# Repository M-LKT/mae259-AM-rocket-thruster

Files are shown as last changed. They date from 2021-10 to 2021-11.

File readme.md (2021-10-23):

# Goals for today

- Discussing Rocket Sizing Theory

- Determining Sizing Constraints for Rocket
    - Vehicle size (thrust)
        - Fully Fueled Mass
            - 1200 + 100 + 100 = 1400 t = 1,400,000 kg
        - Lenght
            - Length 50 m
            - Diameter 9 m

        - 0.3 rad/s^2

    - Machine print size (dimensions)
        - LaserTec 65
            - 28.9 in
            - 25.6 in
            - 22 in
            - 1322 

- Chemsitry
    - Propellants
    - Pressure

- Engine Contour Sizing
    - Chamber contour
    - Parabolic nozzle
    - Estimate for heat transfer

# Notes

Types of propellants

## Fuels (when with LOX)

- Kerosene (250-350s)
- Liquid Methane (300-380s)
- Liquid Hydrogen (400-460s)

- UDMH [Hydrazine] (250-300s)
    - monoprop (150-200s)

## Oxidizers

- Liquid Oxygen
- H202
- N20

- N2H4 [Dinitrogen Tetroxide]

# Assumptions about modeling rocket engine

- Isentropic process
- Use the Area-Mach equation to correlate gas properties throughout nozzle as a function of cross-sectional area (depends on isentropic gamma ratios)

- exhaust velocity equation

# Contour

Generated Contour
- Has regen section and a radiative nozzle extention section
- config file for RPA (evaluative copy)

Contour represents the inner surface of the rocket engine that our chamber has to meet.

# Components and CAD

For a summary of best practices and different design types, reference [This NASA Report](https://ntrs.nasa.gov/api/citations/19770009165/downloads/19770009165.pdf)

## Cooling regimes

We are choosing two cryogenic propellants in an autogenous pressurization scheme for in-space service. Therefore, the rocket engine has three distinct chamber sections.
- Fuel Jacket (LCH4 cooled section)
- Oxidizer Jacket (LOX cooled section)
- Nozzle extension (radiatively cooled high emmisivity coated refractory metal section)

The rocket engine heat supplies the energy needed to maintain pressure in the tanks. The control valves that actually feed propellant vapor back to the tanks is not in the scope of this project, so we will roughly estimate how much heat is needed for each propellant and design the cooling sections lengths based on that and an estimate of heat flux through the engine.

    Propellants recieve an equal ratio of total Q per their heat of vaporization. Where Q_fuel/h_vap_LCH4 = Q_ox/h_vap_LOX

Fuel is typically used in the chamber while a secondary oxygen section is added in the nozzle. Each section will have its own inlet and outlet, and its own cooling channel geometry.

## Chamber design

The chamber will roughly be composed of two material layers.

- Inner wall (with cooling channel geometry)
- Outer wall

### Inner wall

The inner wall needs to maintain a heat flux from the hot gases into the coolant fluid (LCH4 or LOX). It also needs to maintain pressure (the cooling jacket is approximately 20-30% higher pressure than the chamber due to injector pressure drop) in the jacket. The design parameters are:

- Material choice
    - High conductivity
    - High service temperature
    - High yeild strength at temperature (for thinness)
- Material thickness (or thickness profile)
    - Thinner = more heat flux

Material needs to also be alloyable with the outer wall material or they need to be the same material.

Cooling channel design is a complex problem, so we will simplify it basing the thickness on the worst case heating and bulk energy capacity without considering convective or cold side boundary layer effects (like nucleate boiling). With this simplification, the cooling channel design parameters become:

- Cooling channel width
- Cooling channel height (also expressible as an aspect ratio of width)
- Number of cooling channels

As mentioned above, the cooling channels must support the max expected heat flux at the worst point and the fluid must be able to support the bulk energy gain throughout the jacket without exceeding the boiling point at pressure. Jacket pressure drop effects and multiphase flow will not be considered.

### Outer wall

The outer wall is basically the pressure bearing structure of the chamber. It is optimized for weight. Design points:

- Material choice
    - Strength to weight ratio
- Material thickness

A safety factor of 1.15 is standard in stress. Loading condition: hoop stress, combined non-uniform pressure vessel stress. Vibration effects neglected.

## Inlet Outlet

Fuel jacket inlet is a external manifold at the bottom of the cooling section
Fuel jacket outlet is an internal manifold at the top of the engine to interface with injector

Oxidizer jacket inlet is an external manifold at the bottom of the printed engine
Oxidizer jacket outlet is an external manifodl at the top of the cooling section

Manifolds need to have a tapered profile to reduce static pressure variation over the jacket crossection.

## Nozzle extension

The nozzle extension design points are:
- Material choice
- Material thickness (or variable thickness profile)
- Coating material and thickness

These three parameters govern maximum equillibrium temperature, the pressure stress, and the thermal expansion stress on the components.

## Nozzle extension interface

The nozzle extension interface is the attach method between the 3D printed chamber and the nozzle extension. Roughly speaking, it needs to:

- Be manufacturable and easy to assemble with a semi-automated method
- Form a gas-vaccuum seal (pressure differential of less than 1 atm)
- Be thermally-compatible: maintain seal and not over-stress either component during the thermal expansion of the nozzle.
- Needs to withstand vibration and be flight-certifiable (if using fasteners, need lockwire probably)

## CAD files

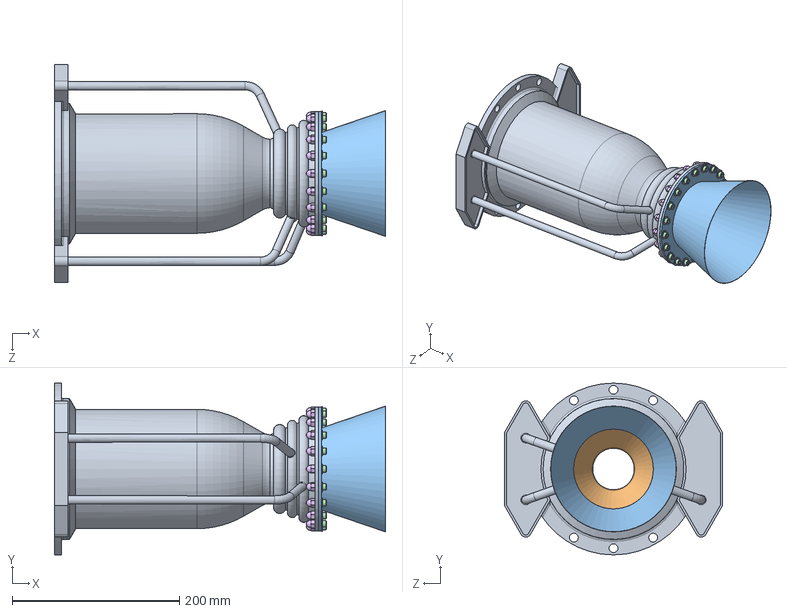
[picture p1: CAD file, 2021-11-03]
CAD_Models/Engine_Assembly.SLDASM
395.8 x 205.5 x 260.7 mm
Chamber - Outer
Chamber - Inner
Extension Nozzle
socket head cap screw_ai x 20
flat washer type a selected narrow_ai x 20
acorn low crown nut_ai x 20

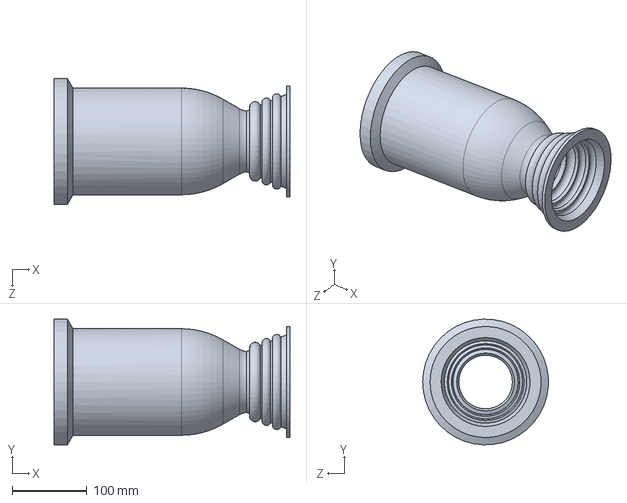
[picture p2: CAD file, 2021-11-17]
CAD_Models/DED_Adjustments/DED - Chamber - Outer.SLDPRT
315.9 x 168.3 x 168.2 mm

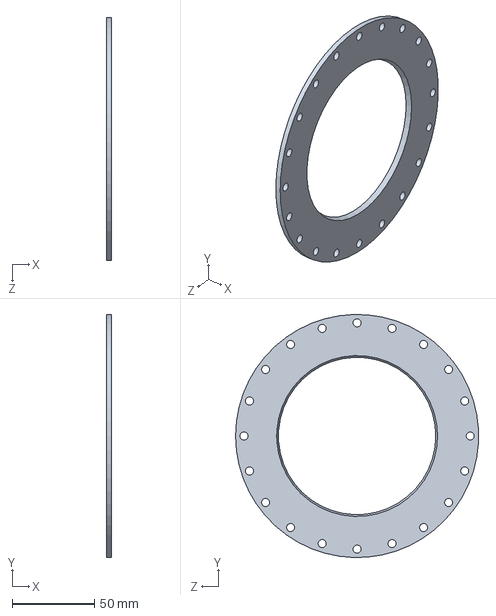
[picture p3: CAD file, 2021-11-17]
CAD_Models/ExtensionNozzleFlange_Cam.SLDPRT
3.17 x 148.1 x 148.1 mm

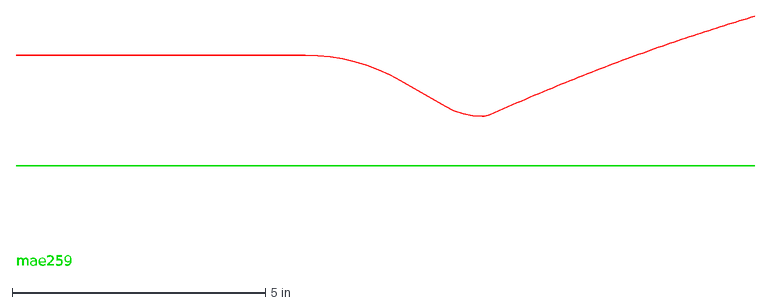
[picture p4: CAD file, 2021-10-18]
rpa-contour.dxf
mae259

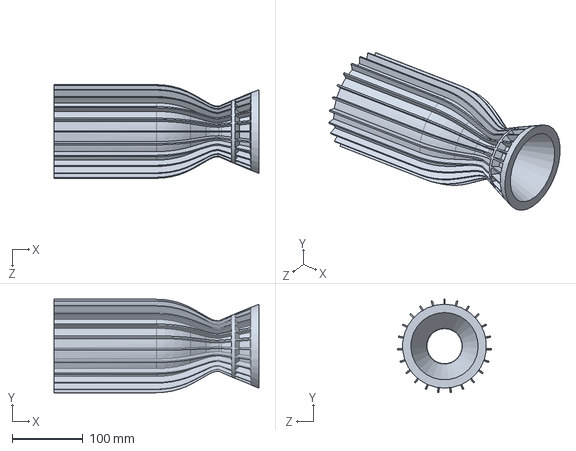
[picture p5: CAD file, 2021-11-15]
CAD_Models/Chamber - Inner.SLDPRT
290.5 x 132.5 x 132.8 mm

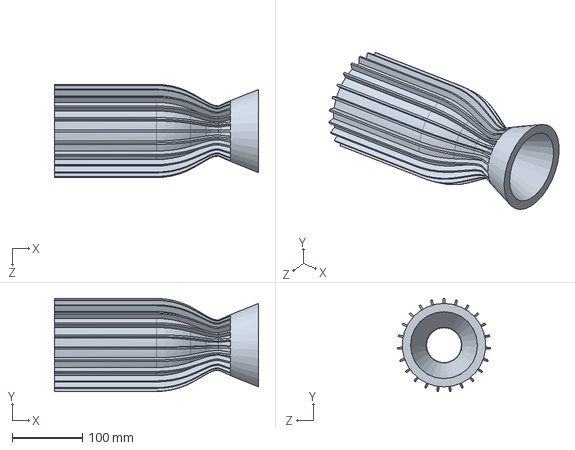
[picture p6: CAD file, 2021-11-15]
CAD_Models/DED_Adjustments/DED - Chamber - Inner.SLDPRT
290.5 x 132.5 x 132.8 mm

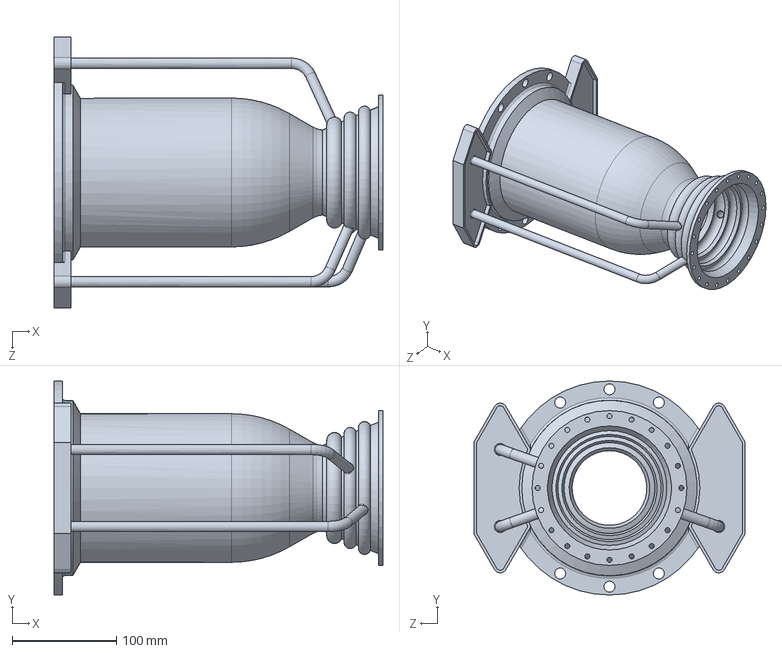
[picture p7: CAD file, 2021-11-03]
CAD_Models/Chamber - Outer.SLDPRT
315.9 x 205.5 x 260.7 mm

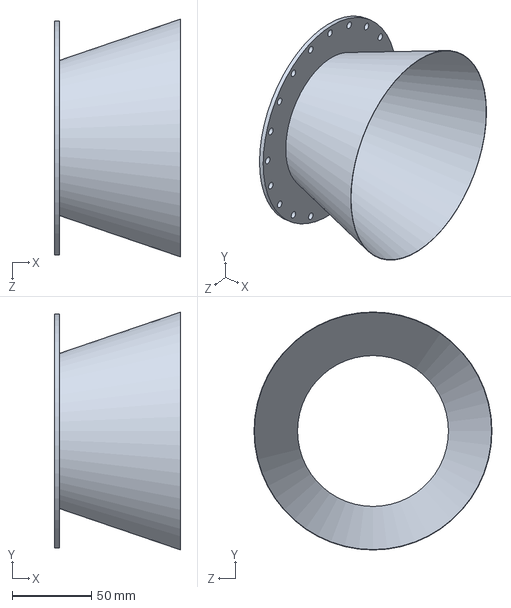
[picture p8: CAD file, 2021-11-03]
CAD_Models/Extension Nozzle.SLDPRT
80.0 x 150.4 x 150.4 mm

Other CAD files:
CAD_Models/contour.SLDPRT

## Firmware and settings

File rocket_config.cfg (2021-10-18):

version = 1.3;
name = "mae259";
info = "";
generalOptions : 
{
  multiphase = true;
  ions = true;
  flowSeparation = true;
};
combustionChamberConditions : 
{
  pressure : 
  {
    value = 6.0;
    unit = "bar";
  };
};
nozzleFlow : 
{
  calculateNozzleFlow = true;
  nozzleInletConditions : 
  {
    contractionAreaRatio = 5.0;
  };
  nozzleExitConditions : 
  {
    pressure : 
    {
      value = 0.1;
      unit = "atm";
    };
  };
  nozzleStations = ( );
};
propellant : 
{
  components : 
  {
    ratio : 
    {
      value = 3.1;
      unit = "O/F";
    };
    oxidizer = ( 
      {
        name = "O2(L)";
        massFraction = 1.0;
        p : 
        {
          value = 0.0;
          unit = "MPa";
        };
      } );
    fuel = ( 
      {
        name = "CH4(L)";
        massFraction = 1.0;
        p : 
        {
          value = 0.0;
          unit = "MPa";
        };
      } );
  };
};
engineSize : 
{
  thrust : 
  {
    value = 2.0;
    unit = "kN";
  };
  ambientConditions : 
  {
    value = 0.0;
    unit = "atm";
  };
  chambersNo = 1;
  chamberGeometry : 
  {
    length : 
    {
      value = 1.0;
      unit = "m";
    };
    characteristicLength = true;
    contractionAngle = 30.0;
    R1_to_Rt_ratio = 1.5;
    Rn_to_Rt_ratio = 0.382;
    R2_to_R2max_ratio = 0.5;
  };
};
chamberCooling : 
{
  heatTransfer : 
  {
    relationsType = "Bartz";
    applyBLC = false;
    numberOfStations = 50;
    radiationHeatTransfer : 
    {
      hotSideWallSurfaceEmissivity = 0.8;
    };
    wallLayerHeight = 0.025;
  };
  chamberCoolingSections = ( );
  filmSlots = ( );
};
propelantFeedSystem : 
{
  estimateDryMass = false;
};

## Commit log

2021-10-18 contour draft + rpa file
    [contour.SLDPRT, rocket_config.cfg, rpa-contour.dxf]
2021-10-20 finished contour design
    [contour.SLDPRT, contour_long.SLDPRT]
2021-10-23 design plan update
    [contour_long.SLDPRT]
2021-10-28 Update mae252_rocket_engine_project.m
    Added calculation for the heat flux qw and code to print out the dimensions of the cooling channel.
2021-10-28 Create Chamber - Outer.SLDPRT
    Started modeling the outer shell of the chamber. Aiming to match one of the pics Makar dropped in Discord when we met on Monday. Offset 2mm from where I expect inner wall/ribs to be but can adjust as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
    [Chamber - Outer.SLDPRT]
2021-10-29 Update Chamber - Outer.SLDPRT
    Added the "base" for mounting. Need to model inlet/outlet. Going to look into more doc's on this. I believe (2) need to attach to the nozzle?
    [Chamber - Outer.SLDPRT]
2021-10-29 Added Cooling Channels
    Added cooling channels to the rocket engine. Redid some sizing with parametric modeling. Inner-wall thickness, outer-wall thickness, cooling channel dimension, number of cooling channels can be chang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
    [Chamber - Cooling Channel.SLDPRT, Chamber - Outer.SLDPRT]
2021-10-29 added materials + started assembly
    [Chamber - Cooling Channel.SLDPRT, Chamber - Outer.SLDPRT, Engine_Assembly.SLDASM]
2021-10-29 Reconstructed Outer Geometry
    Reconstructed the outer geometry on the rocket engine with cooling channel based off of the previous geometry in Chamber - Outer part.
    [Chamber - Cooling Channel.SLDPRT]
2021-10-29 Moved Solidworks Files to CAD Folder
    [Chamber - Cooling Channel.SLDPRT, Chamber - Outer.SLDPRT, Engine_Assembly.SLDASM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]
2021-11-01 Update Chamber - Outer.SLDPRT
    Fixed the inner diameter issue so it should align with the cooling channels now. Added the inlet/outlet holes for now. Currently thinking fuel dia. will be 22.2mm and Ox dia. will be 11.1mm
    [Chamber - Outer.SLDPRT]
2021-11-02 Updated Chamber
    Updated chamber inner wall and cooling channel geometry, and added a rib seperating the 2 coolants.
    [Chamber - Cooling Channel.SLDPRT, Chamber - Inner.SLDPRT, Chamber - Outer.SLDPRT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]
2021-11-02 Update Chamber - Outer.SLDPRT
    Updated manifolds to prepare for inlet/outlet. Added potential chamber for connection below nozzle extension cutoff. Added prelim interface, not sure of sizing
    [Chamber - Outer.SLDPRT]
2021-11-02 Update Chamber - Outer.SLDPRT
    Trying to update this darn file lol
    [Chamber - Outer.SLDPRT]
2021-11-02 Update Chamber - Outer.SLDPRT
    Added in all 3 flow channels, made sure they're hollowed out. Should be good for "final" assembly unless other changes are required
    [Chamber - Outer.SLDPRT]
2021-11-02 Create Extension Nozzle.SLDPRT
    Cad for Extension Nozzle
    [Extension Nozzle.SLDPRT]
2021-11-02 Moved rib location
    [Chamber - Inner.SLDPRT, Chamber - Outer.SLDPRT, Engine_Assembly.SLDASM]
2021-11-02 Update Engine_Assembly.SLDASM
    Nozzle Added
    [Engine_Assembly.SLDASM]
2021-11-02 added material properties to nozzle extension
    [Engine_Assembly.SLDASM, Extension Nozzle.SLDPRT]
2021-11-02 Update Chamber - Outer.SLDPRT
    Added holes to nozzle interface
    [Chamber - Outer.SLDPRT]
2021-11-03 Adjust the hole for fasteners
    [Chamber - Inner.SLDPRT, Chamber - Outer.SLDPRT, Engine_Assembly.SLDASM]
2021-11-03 applied copper to inner chamber
    [Chamber - Inner.SLDPRT]
2021-11-03 Include Fasteners
    [Chamber - Inner.SLDPRT, Chamber - Outer.SLDPRT, Engine_Assembly.SLDASM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]
2021-11-03 Reapplied copper to inner chamber
    [Chamber - Inner.SLDPRT, Engine_Assembly.SLDASM]
2021-11-03 Added coolant tubes
    [Chamber - Inner.SLDPRT, Chamber - Outer.SLDPRT, Engine_Assembly.SLDASM]
2021-11-03 Added fillets cooling pipes
    Added 1mm fillets to the cooling pipes.
    [Chamber - Inner.SLDPRT, Chamber - Outer.SLDPRT, Engine_Assembly.SLDASM]
2021-11-15 Modified rocket engine geometry for DED
    [Chamber - Inner.SLDPRT, DED - Chamber - Inner.SLDPRT, DED - Chamber - Outer.SLDPRT]
2021-11-17 G-Code for DED
    [DED - Chamber - Outer.SLDPRT]
2021-11-17 Flange CAM
    [ExtensionNozzleFlange_Cam.SLDPRT]
2021-11-17 Update Cam Parameters
    [ExtensionNozzleFlange_Cam.SLDPRT]
